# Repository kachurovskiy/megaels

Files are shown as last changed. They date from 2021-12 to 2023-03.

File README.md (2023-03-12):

**This software and instructions are provided as is, without warranty of any kind. This is a hobby project. Using this might damage your equipment, cause injury or death. Use at your own risk. Original author didn't state the lisence for the code so it remains unknown.**

# MegaEls

Metal lathe electronic lead screw project built on top of Russian-speaking [DigitalFeed ELS system by Oleg A. and contributors from ChipMaker.ru](https://www.chipmaker.ru/topic/118083/).

megaels-example

## ⚡ Looking for resellers and manufacturers 💲

If you're willing to manufacture this device and/or sell it as a kit, we'd be happy to link to your page for free - especially if it makes the build cheaper than buying all the components separately.

## Code

Code is provided in the [folder above](https://github.com/kachurovskiy/megaels/tree/main/Digital_Feed_7e2). It requires tuning a few constants at the top of `Digital_Feed_7e2.ino` to fit your lathe and motors.

Verify that hardware parameters are set correctly:

- Use `mm/min` mode and a clock to ensure each axis moves in the right direction and by the expected amount of mm within 60 seconds
- Use "Dividing head" mode (last one) to check that when you turn the spindle by hand in the "forward" direction, angle on screen increments from 0 to 360

Every time hardware parameters change, update `Cone_Info` and `Thread_Info` tables in the middle of that file using calculator in [`tables.html`](https://kachurovskiy.github.io/megaels/Digital_Feed_7e2/tables.html). If you don't recalculate those tables, your threads and cones will come out wrong even when `mm/min` and dividing head tests above pass.

To upload the code to your device, install Arduino IDE, connect your Arduino Mega to the computer via a USB cable, open `Digital_Feed_7e2.ino`, select `Arduino Mega 2560` in `Tools > Board` and click `Sketch > Upload`.

## PCB

megaels_2012-12-05

[Gerber files for production](https://github.com/kachurovskiy/megaels/raw/main/PCB_20211205/Gerber_PCB_MegaEls_20211205.zip)

Some PCB production techniques use lead and other nasty stuff. Order at your own risk and dispose properly.

Ordering it from JLCPCB.com takes just a few clicks - upload the ZIP file, use all default settings, choose shipping and checkout. Costs around 20 euro with delivery for 5 PCBs (minumum order).

## Components

- [Arduino Mega 2560](https://www.aliexpress.com/item/32850843888.html) (micro USB)
- [Connector pins](https://www.aliexpress.com/item/1005002577212594.html) that would get soldered to the board
- [1602 LCD 5V](https://www.aliexpress.com/item/32326489466.html)
- [9 6\*6 push buttons](https://www.aliexpress.com/item/32862548214.html)
- [8-position switches](https://www.aliexpress.com/item/4000700310059.html)
- [Manual pulse generator 5V 4-pin 100 pulses](https://www.aliexpress.com/item/32949618549.html) 60mm
- [4-position joystick with latching and a button](https://www.aliexpress.com/item/4000893010190.html) though this one is a little too big and hard to switch
- [2 RV09 10kOhm potentiometers](https://www.aliexpress.com/item/4000078097697.html)
- [KF2EDG connectors with 3.5mm pitch](https://www.aliexpress.com/item/1005003085954456.html) - 5 with 4 pins, 1 with 6 pins, make sure to order both plug and straight needle
- [4 1kOhm resistor arrays with 8 resistors each](https://www.aliexpress.com/item/32840103807.html)
- 2 1kOhm resistors and 4 680 Ohm resistors
- 5V buzzer
- 2 ceramic capacitors e.g. 10 uF
- 4 LEDs

## Cases

The following cases are designed to be used with [M3 threaded inserts](https://www.aliexpress.com/item/32430148405.html) that would be pushed into the 4 designated holes using your soldering iron tip and receive M3 [nylon screws (for MPG) or 20mm standoffs (for the main case)](https://www.aliexpress.com/item/32617866125.html). 

### Main case

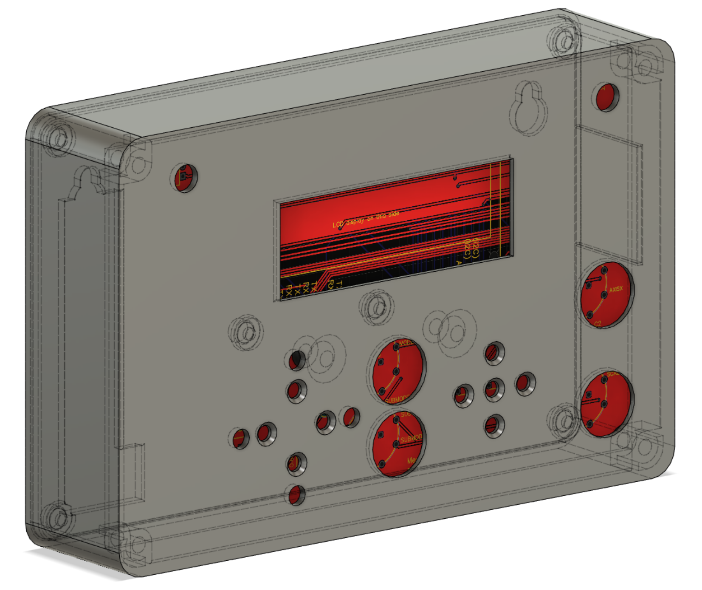
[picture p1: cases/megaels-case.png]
megaels_2012-12-05


Here the lid is connected using nylon screws into 20mm standoffs that work as screws holding the PCB down. It's designed to be mounted using two M5 bolts 135mm apart on centers.

Cut 1 line on the right side of the case and push the small part of the wall to the outside to get access to the mini USB port of the Arduino.

Download: [STL body](https://github.com/kachurovskiy/megaels/raw/main/cases/megaels-case-body.stl) and [STL lid](https://github.com/kachurovskiy/megaels/raw/main/cases/megaels-case-lid.stl) or [f3d](https://github.com/kachurovskiy/megaels/raw/main/cases/MegaElsCase.f3d)

[Printable SVG](https://github.com/kachurovskiy/megaels/raw/main/megaels-face.svg) with labels for the controls.

### MPG case

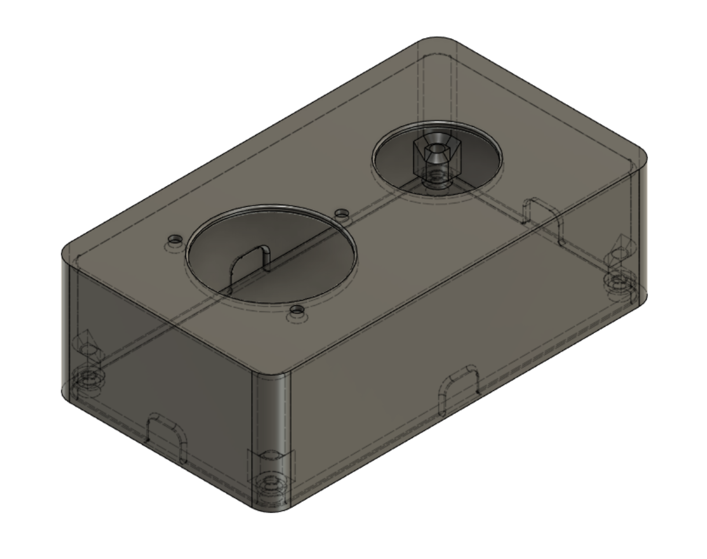
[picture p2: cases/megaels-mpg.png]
megaels_2012-12-05


Download: [STL body](https://github.com/kachurovskiy/megaels/raw/main/cases/megaels-mpg-body.stl) and [STL lid](https://github.com/kachurovskiy/megaels/raw/main/cases/megaels-mpg-lid.stl) or [f3d](https://github.com/kachurovskiy/megaels/raw/main/cases/MegaElsMPG.f3d)

## Schematics

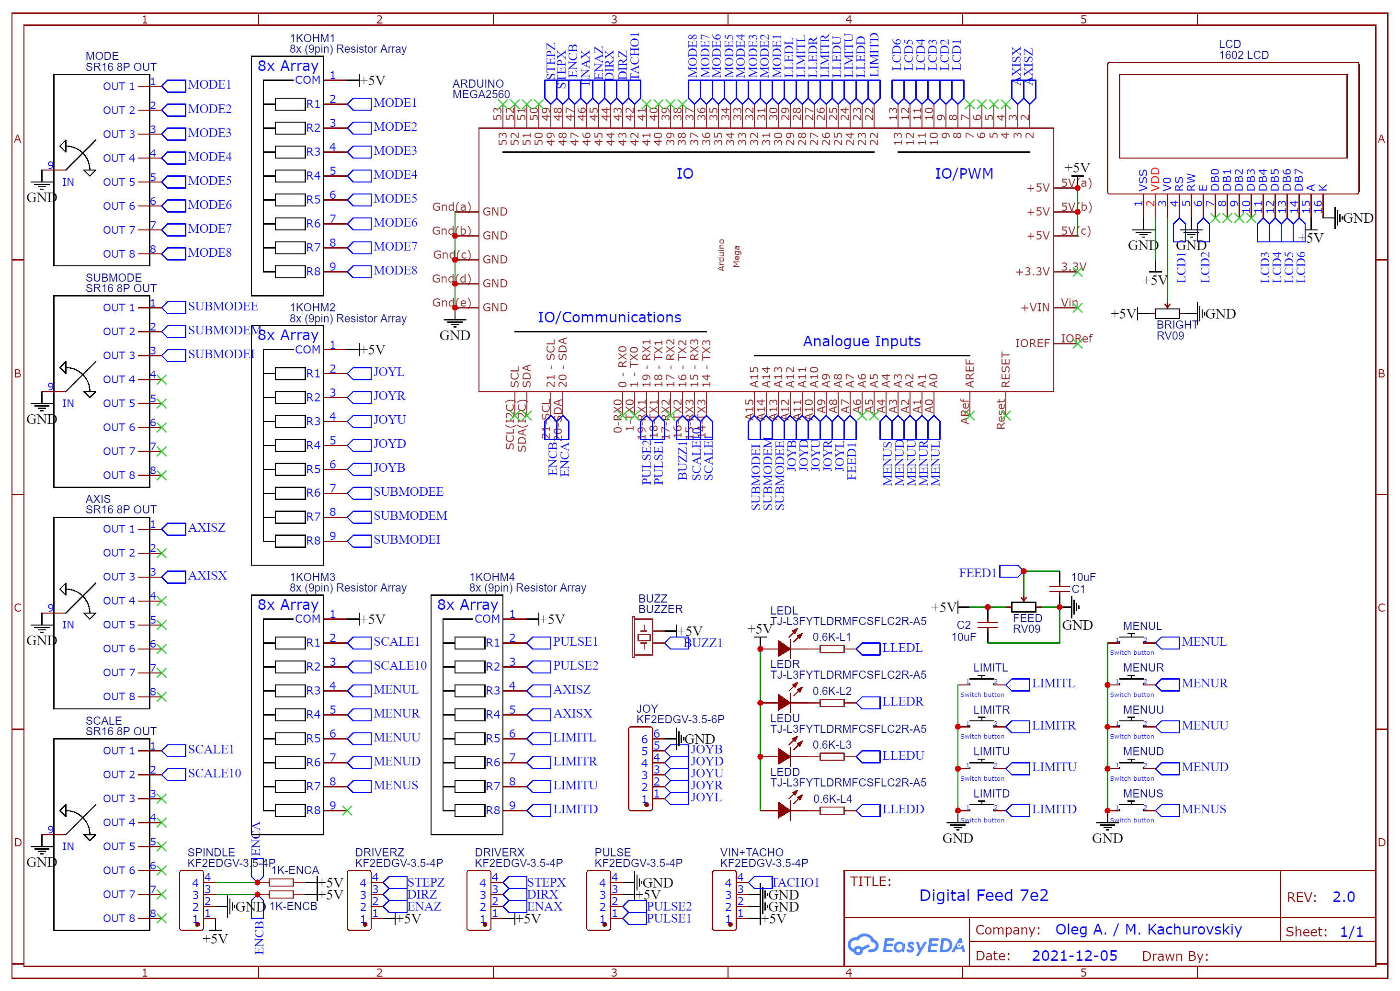
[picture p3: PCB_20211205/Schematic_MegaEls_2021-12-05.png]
MegaEls schematics


## Quick Start

### Moving the tool

- Select `Z` or `X` axis using the corresponding switch
- Select `1x` or `10x` scale using the corresponding switch
- Rotate the handwheel

https://user-images.githubusercontent.com/517919/150657985-6fe1d571-e0b5-475b-9b13-4543c2c39b69.mp4

1 impulse from the handwheel should correspond to 0.01mm movement of the motor in `1x`, 0.1mm in `10x`. If the motor doesn't move, try switching to submode to manual or switching mode to a different value.

### Turning of facing

https://user-images.githubusercontent.com/517919/150658372-34b87c6c-d6d8-46ef-8bb0-31651cf59bb8.mp4

- Set mode to `Feed mm/rev`
- Set submode to manual
- Start the spindle
- Use joystick to start/stop feeding into any of the 4 directions
- Use the top-left potentiometer to change the speed

### Asynchronous feed (grinding)

https://user-images.githubusercontent.com/517919/150658051-4663ad40-8815-415f-8046-cac0e11eda6a.mp4

- Set mode to `Feed mm/min`
- Set submode to manual
- Use joystick to start/stop feeding into any of the 4 directions
- Use the top-left potentiometer to change the speed.

### Threading

Using the right-hand thread cut to the chuck as an example:

https://user-images.githubusercontent.com/517919/150672370-4f7bad88-6a53-406b-a333-fa034ceace00.mp4

- Set mode to `Thrd`
- Set submode to manual
- Use up/down menu buttons to select the pitch. For TPI pitches, scroll up through all the metric pitches.
- Move the tool using the handwheel to the left-most `Z` position
- Set the left limit using the corresponding button
- Move the tool using the handwheel to the right-most `Z` position
- Set the right limit using the corresponding button
- Start the spindle
- Move in the cutter (manually or using the handwheel)
- Set joystick to "left" and wait for the tool to reach the left limit (don't stop the spindle)
- Move the cutter out
- Set joystick to "right" and wait for the tool to reach the right limit (don't stop the spindle), use joystick button for faster movement
- Move in the cutter
- Set joystick to "left" and so on

### Automatic threading

Using the right-hand thread cut to the chuck as an example:

https://user-images.githubusercontent.com/517919/150673123-4970087e-299d-4873-bf87-a3d265480593.mp4

- Set mode to `Thrd`
- Set submode to manual
- Use up/down menu buttons to select the pitch. For TPI pitches, scroll up through all the metric pitches.
- Move the tool using the handwheel to the left-most `Z` position
- Set the left limit using the corresponding button
- Start the spindle
- Move the tool using the handwheel so that the cutter just barely touches the material
- Move the tool using the handwheel to the right-most `Z` position
- Set the right limit using the corresponding button
- Set submode to external
- Set joystick to "left" and wait for the operation to complete

When done, set joystick to neutral and submode to manual to be able to use the handwheel again.

#### Manual follow-up after automatic threading

When automatic threading is finished you can test fit and potentially make a few more passes:

https://user-images.githubusercontent.com/517919/150681412-96608c69-1e91-40f1-9b8f-9cf68e4d7d45.mp4

- Move joystick to neutral
- Set submode to manual
- Set joystick to "right" and press the joystick button to move past the right limit
- Turn on the spindle (no need to reverse it) and wait for the cutter to move out of the way, turn off the spindle
- Test fit the part
- Set joystick to "left"
- Turn on the spindle, move in the cutter, make another pass, it should stop at your existing left stop
- Move out the cutter, no need to stop the spindle
- Set joystick to "right", it should stop at your existing right stop, repeat until the part fits

### Cones

https://user-images.githubusercontent.com/517919/151621173-53c0f2e1-b2ff-46d9-8cfa-94ba974be943.mp4

- Set mode to `>` or `<`
- Set submode to manual
- Pick the cone angle using the menu buttons
- Turn on the spindle
- Use joystick "left" and "right" positions to move the cutter along the cone
- Use joystick "forward" and "back" positions to move the cutter in or out

## Manual

There are [some instructions explaining how to operate the ELS](https://github.com/kachurovskiy/megaels/blob/main/Digital_Feed_7e2/manual.md) that I auto-translated and corrected a bit but expect to invest some time here :)

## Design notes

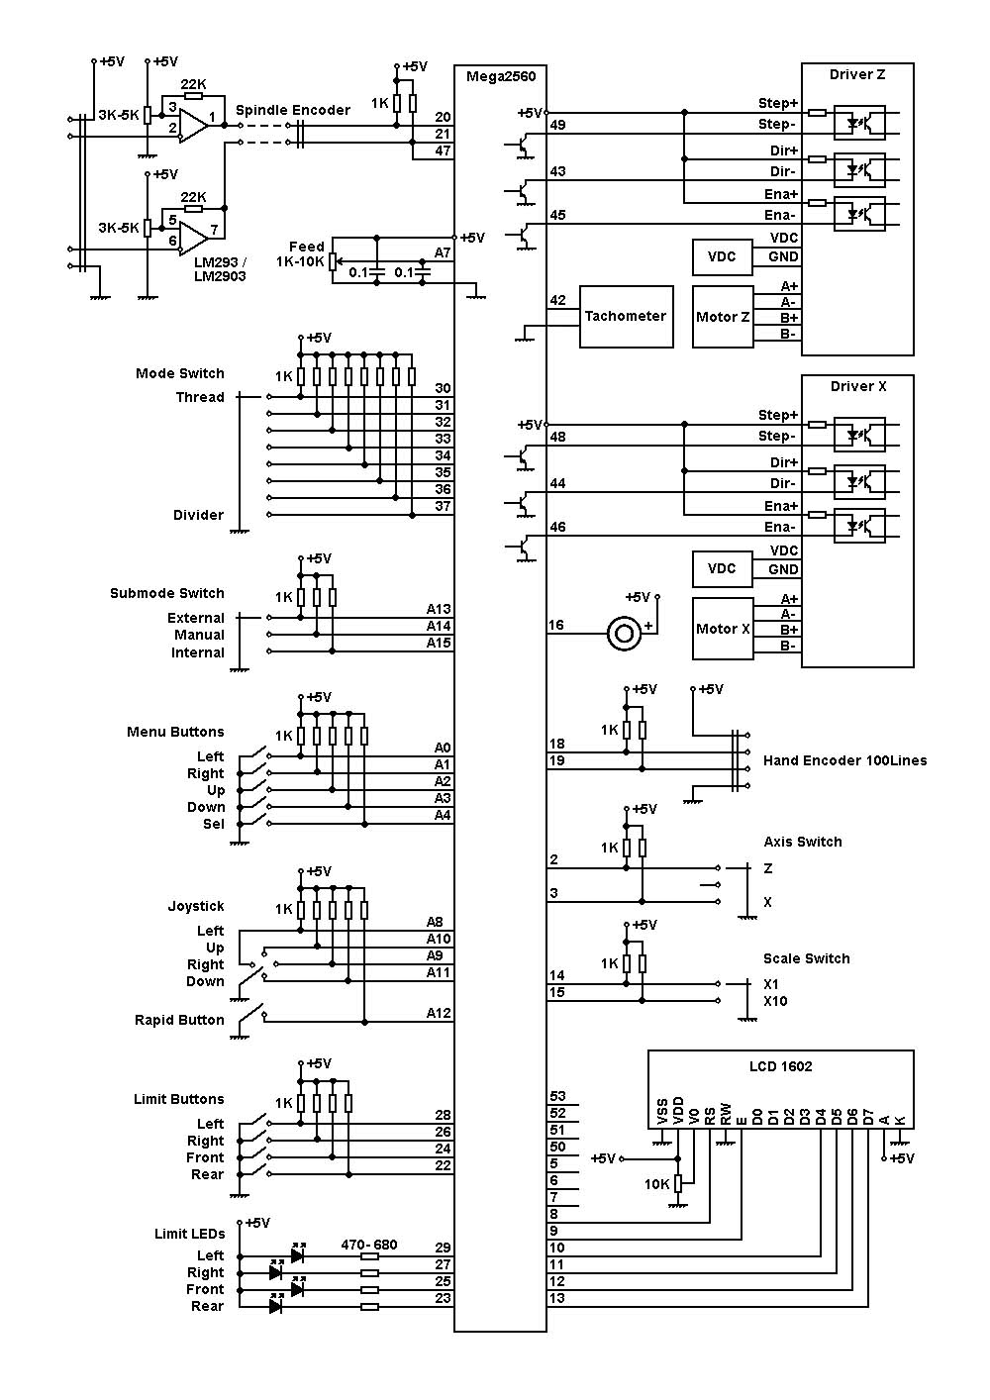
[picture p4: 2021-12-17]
Digital_Feed_7e2/!_ELS_V7.jpg

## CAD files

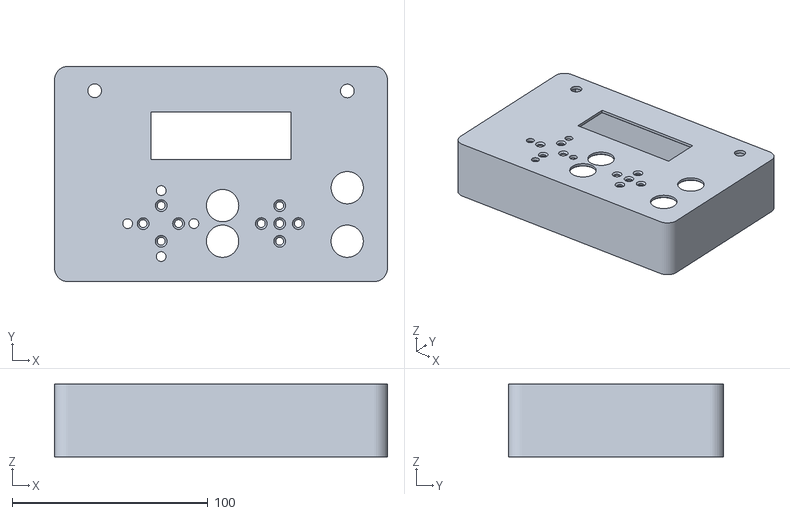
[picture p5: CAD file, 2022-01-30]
cases/megaels-case-body.stl
170.0 x 110.0 x 37.1

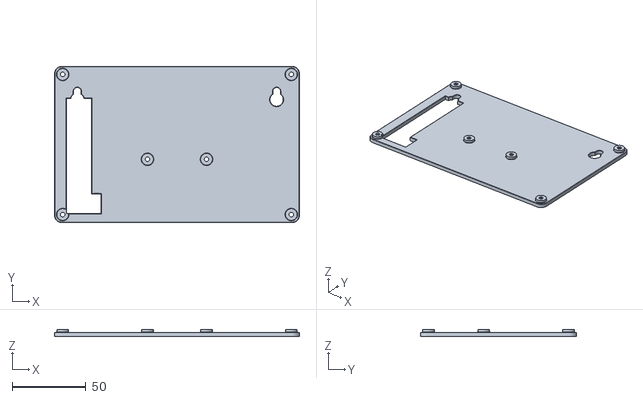
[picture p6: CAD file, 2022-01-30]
cases/megaels-case-lid.stl
166.0 x 106.0 x 5.00

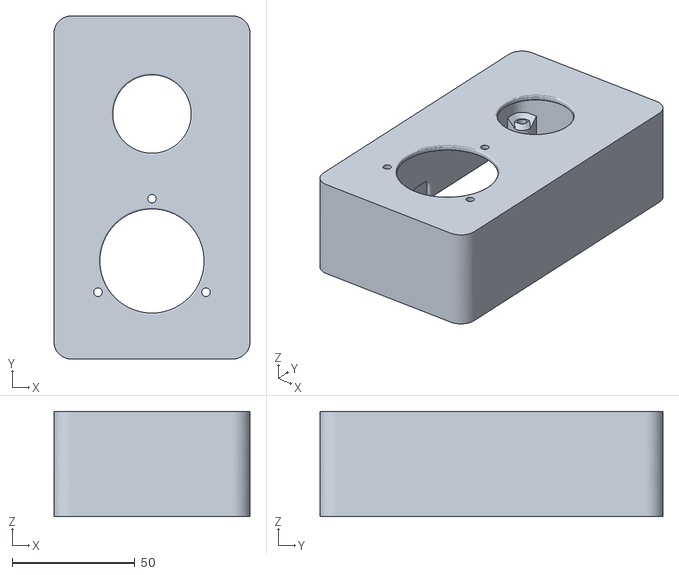
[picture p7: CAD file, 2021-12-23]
cases/megaels-mpg-body.stl
80.0 x 140.0 x 43.0

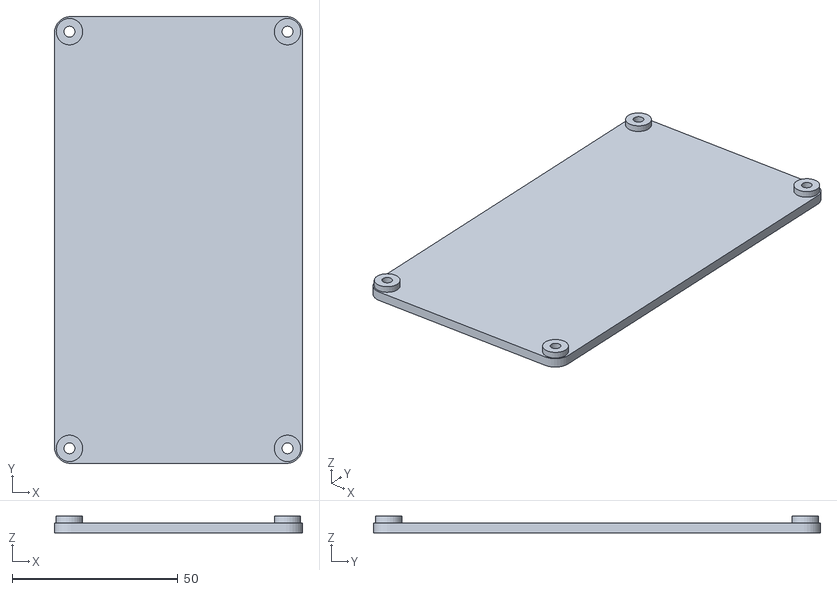
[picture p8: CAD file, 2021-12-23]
cases/megaels-mpg-lid.stl
75.0 x 135.0 x 5.00

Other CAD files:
cases/MegaElsCase.f3d
cases/MegaElsMPG.f3d

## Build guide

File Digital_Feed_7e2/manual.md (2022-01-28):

# Digital Feed Electronic Lead Screw 7e2 Manual

Note: this is a slightly redacted automated translation of a manual written by Oleg A. and contributors from ChipMaker.ru. Use with caution.

## Basic concepts and definitions

**Limits** (electronic stops) are virtual positions on the workpiece that limit the machining area (movement ranges tool) and operate in different modes of operation. There are left, right, front and back limits. 

The positions of the limits are set only with the middle (neutral) position of the joystick and the position of the "Submode" switch "Manual". 

Note: the distance between the limits (processing zones) cannot be less than some values determined by your equipment and firmware parameters (the distance between the limits cannot be less than the "acceleration + deceleration" accelerated).

**Feed** is a value that characterizes the speed of the tool along or across the workpiece. Depending on the mode of operation, synchronous or asynchronous, it is measured in millimeters per revolution or millimeters per minute.

**Rapid feed** is the mode of tool movement with the maximum possible speed along one of the axes. It is activated by pressing a special fast travel button on the joystick. Rapid feed is not activated or the movement does not start at all when the distance from the current position of the tool to the stop on the side of movement is less than the distance required for acceleration and deceleration.

## Controls

### Tuning

Intended for selecting the operating mode and setting the mode parameters:

- 8-position mode switch
- 3-position submode switch
- Buttons - up / down / right / left / select to select and change parameter values

### Operational

Directly for operation:

- 4-position joystick with position fixation and its "rapid feed"
- Button 4 buttons for setting / removing limits (left / right / front / rear)
- Potentiometer, which sets the amount of feed to the manual pulse generator (popularly RGI, Handcoder) - 100 pulses per revolution and its satellite switches:
  - 3-position - axis selection: Z / inactive / X
  - 2-position - selection of the scale of movement: 0.01mm / 0.1mm per one "click" of the RGI.

## Basic operating modes

### Thread

- With spindle reversal without opening the mother nut (no limits)
- Without reversing and without opening the nut, switching the direction of the joystick (limits must be set)
- Without reversing with opening the nut and manual return (synchronization by the threaded indicator)
- Automatically (see below)

When preparing and setting the parameters:

- Use the Up-Down buttons to select the thread pitch, can be changed only when the joystick is in a neutral position
- 4 thread directions along the joystick
- 4 limit buttons, limits are set only when the joystick is in neutral position

When the joystick button is pressed, the right stop is ignored, you can arbitrarily ride after it and try on the counterpart, to restore synchronization, it is enough to enter the zone between the limits and reach the right stop, continue threading as usual.

### Automatic threading

1. Prepare outside/inner diameter to the starting size (e.g. 12mm for M12)
2. Set the right and left stops to the required thread length
3. In the "Thread" mode, use the Up / Down buttons to select the required pitch
4. With the "Submode" switch, select "External" Ext or "Internal" Int
5. On the example of a right-hand thread, direct spindle turns, cut to the chuck:
   1. before starting, touch the workpiece with a threaded cutter in diameter and set the carriage to the right stop (limit),
   2. switch the joystick to the left, the process has started, the cross stops light up alternately , the cross stops are extinguished - the process is complete.
6. When done, tool moves to the starting position

**When cutting 55 degree thread, do not use the automatic threading** - or use the machine 2 times in a row, having previously recalculated the height of 55 degree and 60 degree triangles for the current step, before the second pass of the machine, apply the difference in depth manually.

### Multi-start thread

After cutting the 1st thread:

1. Move the cutter to the starting position (in automatic mode, the cutter will take the starting position itself)
2. Stop the spindle
3. Switch to the "Divider" mode
4. Turn the spindle to set the displayed angle to 180 degrees
5. Reset the angle with the "Sel" button
6. Return to the "Thread" mode
7. Start the spindle
8. The 2nd thread will be cut with an offset of 180 degrees relative to the 1st
9. For a 3-way entry - reset accordingly after 120 degrees, etc.

### Synchronous feed (mm / rev)

- 4 directions of feed on the joystick
- 4 directions of rapid movement on the joystick and the button of the accelerated
- 4 buttons of the limit, the limits are set only with the neutral position of the joystick and manual submode

Use the potentiometer on the top-left to change the amount of feed (even during the operation).

### Automatic multi-pass synchronous feed (mm / rev)

Same as "Synchronous feed" but also:

- Use the Up / Down buttons to set the removal rate `Ap`
- Use the Right / Left buttons to set the number of passes `Pq`

Total amount of material removed is `Pq * Ap * 2`.

#### External groove, direction to the chuck

In the "Manual" mode set the right + left limits, move the instrument to the right limit, the "Submode" switch to the "Ext" position, switch the joystick "Left". 

#### External groove, direction from the chuck

In "Manual" mode, set the right + left limits, move the tool to the left limit, switch "Submode" to the "Ext" position, switch the joystick "Right".

#### Internal boring, direction to the chuck

In "Manual" mode set the right + left limits, move the tool to the right limit, switch "Submode" to "Int", switch the joystick "Left".

#### Internal boring, direction from the chuck

In the "Manual" mode set the right + left limits, move the tool to the left limit, switch the "Submode" switch to the "Int" position, switch the joystick "Right".

#### Facing, direction to the spindle axis

In the "Manual" mode, set the front + back limits, move the tool to the back limit, the "Submode" switch to the "Ext" position, switch the "Forward" joystick.

#### Facing, direction from the spindle axis

In the "Manual" mode, set the front + back limits, move the tool to the front limit, the "Submode" switch to the "Ext" position, switch the "Back" joystick.

### Asynchronous feed (mm / min)

- 4 directions of feed along the joystick
- 4 directions of fast movement along the joystick and the accelerated button
- 4 buttons of the limit, the limits are set only with the neutral position of the joystick and neutral the position of the switch "Submode"

Use the potentiometer on the top-left to change the amount of feed (even during the operation).
 
### Automatic multi-pass asynchronous feed (mm / min)

Experimental.

### Cone left and right (Cone < and Cone >)

- Use the Right-Left buttons (with the joystick neutral position) to select the cone.
- The front-back limits (if they were set earlier) are ignored, but their position in memory is retained.
- Cutting is switched on by Joystick Right / Left.
- The joystick button is used to accelerate movement, the trajectory is the selected cone.
- Joystick forward / reverse switching enables synchronized feed in the corresponding direction.

Sharpen the inner cone from a smaller diameter to a larger one, gradually going deeper into the previously prepared hole. Sharpening from the chuck.

Sharpen the outer cone from a larger diameter to a smaller, larger diameter at the chuck.

The exception is the adapter, in this case, too, from a larger diameter to a smaller one, but the chuck has a smaller diameter and is cut in advance.

In this case, the backlash of the screws is taken out and both screws will always be loaded by the feed.

This principle is used to build an Automaton on cones. 

#### Automatic cone

3 variations are available:

- outer cone (thick at the chuck) cut from left to right
- outer cone (thin at the chuck, you need a technological cut along the left end), cut it from right to left, before the technological groove
- inner cone (thin at the chuck) cut it from left to right

### Reserve

Empty for now.

### Rough sphere (Sphr)

Tool - a cut-off tool with a straight cutting edge.

- Using the Up / Down buttons set the diameter of the ball,
- Use the Right / Left buttons to set the residual diameter of the leg,
- With the "Sel" button pressed, set the width of the cutter
- With the "Sel" button pressed, buttons Right / Left set the width steps (step Z)

Procedure:

1. Cut through the workpiece in diameter future sphere + D which must be greater than X backlash and less than REBOUND_X
2. Use parting tool
3. Cut through the workpiece for the convenience of measurements, but no more than ⅓ of the given diameter is not clear in Z or X (with a cutting tool) with measurements in the required diameter of the future ball
4. Engage the rear support
5. Butt the workpiece (dust the end)
6. Return to the back stop
7. Activate the right stop
8. Switch the joystick to the left
9. Wait end of the process
 
### Division of a circle - divider calculator

The first line of the indicator displays the number of division sectors and the required angle for the current sector (Req). The number of division sectors (maximum 255) is set by the Up-Down buttons.

The second line of the indicator displays the number of the current sector, and the real angle of the spindle. Moving between sectors is carried out with the Right-Left buttons.

All that is required is to turn the spindle to match the readings.

Angle zeroing, if necessary, is performed by the 5th menu button.
 
2 short "beeps" in automatic modes means: "I am working", do not put your hands into the rotating mechanism and wait for the end of the process.

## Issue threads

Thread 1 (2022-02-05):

x cross slide questions

pantonvich, 2022-02-05:
question on tables.html - and in general - on my x axis how do I account for the gear ratio from the x-stepper to cross slide screw pitch.
From your thingverse cross slide - it looks like you have a 3x - 54/18 but I'm not seeing that in the digital_feed_7e2 or tables.html code that you have posted. I have a 1mm cross slide but an odd 77/13. I started my els about a year ago and just started working on it again last month. I found your github in the last two weeks - so thanks for posting what you have. I'm not that good with github - so not sure how to correctly tag this

gerritv, 2022-02-05:
You need to calculate the number of steps to revolve the leadscrew one revolution. The motor is usally 200 steps/rev, add in the 77/13 ratio (5.923) to get 1184.6 steps per rev?

pantonvich, 2022-02-05:
thats what I was thinking so I tried setting MOTOR_X_STEP_PER_REV to 1185. I also tried setting the SCREW_X to 17 with motor 200 - but got an error - see below - looks like if I set the MxStep_X to 1 it's not an issue - so I'll try that.

Digital_Feed_7e2:55: error: static assertion failed: Ð?ÐµÐ²ÐµÑ€Ð½Ð¾ Ð·Ð°Ð´Ð°Ð½Ð¾ Ð·Ð½Ð°Ñ‡ÐµÐ½Ð¸Ðµ MAX_FEED
 static_assert(f > 1, "Ð?ÐµÐ²ÐµÑ€Ð½Ð¾ Ð·Ð°Ð´Ð°Ð½Ð¾ Ð·Ð½Ð°Ñ‡ÐµÐ½Ð¸Ðµ MAX_FEED");

kachurovskiy, 2022-02-05:
I prefer changing the leadscrew pitch - using 1:3 reduction on cross-slide with 1.25mm screw I've entered 42 as SCREW_X. That gives something like 1% of error on cross-slide movements in theory but I'll think of something when it becomes a problem 😄

Getting MAX_FEED error means that system wants you to reduce your MAX_FEED constant value (line 23). I believe validation errors like this ensure that the system has time to issue the stepper pulses in all conditions.

kachurovskiy, 2022-02-05:
Another option to make MAX_FEED validation happy is to reduce micro-stepping e.g. from 800 steps per revolution to 400 - or so I believe.

pantonvich, 2022-02-05:
I set it to 200 i.e 1 and and changed the driver to 200- I'm trying to verify what movement I get with 100 clicks from the handcoder ...

pantonvich, 2022-02-05:
so with
#define MOTOR_X_STEP_PER_REV 1185      // X motor steps (cross-slide) - almost always 200, microsteps configured below
#define SCREW_X              100
#define McSTEP_X             1

I get 1mm on the x axis for 100 clicks of the hand coder - is that what I should expect?

kachurovskiy, 2022-02-05:
> I get 1mm on the x axis for 100 clicks of the hand coder - is that what I should expect?

Yes. Or 10 clicks on 10x resolution.

Closed 2022-02-22.

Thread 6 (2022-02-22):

Réglage des paramètres

Dididu12, 2022-02-22:
I come to you because I want to know the different parameters that must be set in the code and what are the different settings for in the photo below. For example:

SCREW_X (42) ??
MOTOR_X_STEP_PER_REV ??
REBOUND_X ??
REBOUND_Z ??

my turn and the same as kachurovskiy if I do the calculation of the x axis so 54/18= 3. (One complete engine revolution =200) So 3x200=600 MOTOR_X_STEP_PER_REV=600??

As soon as I change its parameters MAX_FEED starts to growl He and yet set to 20

I hope here someone can help me thank you
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

pantonvich, 2022-02-22:
He adjusted screw_x. If you make rev =600 adjust screw_x to pitch of screw likely 1mm so set it to 100. Also you might need to set McSTEP_x to 1 - you will need to set the stepper driver to the same. If code still errors out adj the Max_Feed to a lower number. The point of the check is to not overwhelm the stepper motor with steps it can keep up with.

kachurovskiy, 2022-02-22:
Dilan, what is your main and cross-slide leadscrew pitches? Mine are 2.0mm and 1.25mm. Knowing that and your 3:1 reduction on the cross-slide we should be able to tell you which values to put in the code and on stepper drivers. Thank you.

Dididu12, 2022-02-22:
The main screw and 2mm and 1mm for cross carriage

kachurovskiy, 2022-02-22:
Try the following:

```
#define MOTOR_Z_STEP_PER_REV 200      // Z motor steps (leadscrew) - almost always 200, microsteps configured below
#define SCREW_Z              200      // Z (leadscrew) pitch, in hundreds of a mm
#define McSTEP_Z             4        // Z driver microsteps (400 steps = 2, 800 steps = 4, etc)
#define MOTOR_X_STEP_PER_REV 200      // X motor steps (cross-slide) - almost always 200, microsteps configured below
#define SCREW_X              33       // 1.00mm via 3:1 reduction
#define REBOUND_X            200      // X backlash in microsteps
#define REBOUND_Z            200      // Z backlash in microsteps
#define McSTEP_X             2        // Z driver microsteps (400 steps = 2, 800 steps = 4, etc)
```

You would need to also set the main leadscrew driver to 800 steps and cross-slide driver to 400 steps and update tables via [tables.html](http://kachurovskiy.com/megaels/Digital_Feed_7e2/tables.html).

Dididu12, 2022-02-23:
I'm trying this weekend thank you I'll keep you posted on the progress thank you 🤝👍🏼

Dididu12, 2022-02-26:
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
on the construction diagram I do not quite understand how the card is powered. I guess it's with the green terminals, which I can't translate well, the same for the pulse generator and the joystick, which wire goes where?? thank you very much for your help I soon finished assembling the map print

kachurovskiy, 2022-02-27:
> MY QUESTION: CAN I LEAVE IT AS IS?? ITS INFLUENCE ON WHICH SETTING THANK YOU

I think yes for now.

> which wire goes where?

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

> pulse generator

Your pulse generator should have 4 terminals - 5V, ground, and 2 signal lines. Connect them correspondingly to 5V, ground and 2 remaining pins in the 5th terminal block (counting from the top).

> joystick

For the joystick that is recommended for the build, you need to connect together the wires so that clicking the joystick button or switching it in a given direction connects the corresponding pin on the 6th terminal block to the GND.

E.g. leaning joystick to the left should result in the following 2 pins getting connected:

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

Dididu12, 2022-02-27:
Thank you for your help I think I have understood everything now it's a great job again thank you

Dididu12, 2022-03-01:
Hello everyone before assembling my print card I wanted to test the stop LEDs it turns out that there is one that does not light up the bottom one how to test it in operation with the m card

Dididu12, 2022-03-19:
hello I have just tested the operation of the card it turns out that it does not work as expected I do not know why I have respected the connections well I hope to find a solution

Dididu12, 2022-03-19:
https://user-images.githubusercontent.com/97460665/159134854-392a5770-ab21-449f-872d-c335e52fd27b.mp4

Dididu12, 2022-03-19:
is there a way to weld the yellow resistors and the long black ones thank you

kachurovskiy, 2022-03-19:
Dilan, can you please post the photos of your soldered PCB top and bottom sides? Some easy pitfalls:

- Soldering 10-leg resistors array wrong way
- Soldering LEDs wrong way

What about 8-position switches - do they work as intended? Also, brightness and feed potentiometers?

Dididu12, 2022-03-19:
Je vous envoie la photo demain merci pour la réponse 👍🏼

Dididu12, 2022-03-19:
There is not much that works the stops do not work the 8 position works when they want and the division mode is missing too

Dididu12, 2022-03-19:
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

Dididu12, 2022-03-20:
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

the joystick button doesn't work

kachurovskiy, 2022-03-20:
Dilan, looks like you've soldered the 9x resistor arrays the wrong way? IIRC the dot on the array should be over the square hole on the PCB. In other words, resistance between square hole and all other holes should be 1kOhm.

Dididu12, 2022-03-20:
yes the problem was there but on the other hand the leds do not light up when you press the button any idea??

kachurovskiy, 2022-03-20:
That is expected when the resistor array is connected incorrectly.

Dididu12, 2022-03-20:
this also happens with array resistors in the right direction so it doesn't work yet??

kachurovskiy, 2022-03-20:
Dilan, were you able to de-solder all 40 pins and swap the resistor arrays around? Can you post a photo of how it looks now? Many thanks.

Dididu12, 2022-03-20:
ok I'm not at home my evenings I send you his thank you and yes I unsoldered and exchanged the black resistors

Dididu12, 2022-03-20:
Everything seems to be back to normal, however the sphere mode does not work, that's normal

Dididu12, 2022-03-21:
Hello I have just noticed that the stops are reversed especially the axes how to fix this thank you

kachurovskiy, 2022-03-21:
Dilan, it sounds like you need to check the settings:

1. Go into the last mode (where the spindle angle is shown on screen) and rotate the spindle normally. Angle on screen should increment from 0 to 360 when you make a full turn of the spindle by hand.
2. Go into `Feed mm/min` mode, ensure both axes more in the correct direction. E.g. joystick right results in Z moving right. If not, adjust `Z_INVERT`.
3. Go into `Feed mm/min` mode, use the top-left knob set the speed to e.g. `50`, set joystick to right, use a ruler to ensure the carriage moves 50mm within 60 seconds. Same for X axis. If not, adjust parameters at the top of `Digital_Feed_7e2.ino` until it works.
4. Finally, re-calculate the tables using `tables.html`

Dididu12, 2022-03-22:
ok I'll do it in the weekend I'll let you know

Dididu12, 2022-03-25:
hello my problem and the following the x axis and reverse how to make it rotate in the right direction thank you

Dididu12, 2022-03-25:
![Uploading 16482323569722772504916710016242.jpg…]()

Dididu12, 2022-03-25:
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

Dididu12, 2022-03-25:
I just understood something I realize that as the x axis is inverted this is the problem that's why it doesn't take material it comes back much further each time

kachurovskiy, 2022-03-26:
Dilan, I don't think there's a way to invert X at the moment in the code. Looks like so far no one needed that. Wonder if you happen to have a "reverse" switch on your stepper driver?

Dididu12, 2022-03-26:
I just have the x axis which is reversed I don't know why the connections are well done what to do thank you

gerritv, 2022-03-26:
you can reverse the direction of the motor by exchanging 2 wires, e.g. wires 1 and 2 coming out of the motor.

Dididu12, 2022-03-26:
I tried reversing the wires, it didn't change anything.

gerritv, 2022-03-26:
that is not possible. There are 2 coils in the motor, swapping the two wires for one coil reverses its direction.

Dididu12, 2022-03-26:
ok but which one to exchange do you have a photo thank you

gerritv, 2022-03-27:
This sketch shows wiring in the motor. You need a meter to determine the pairs. (don't worry about which is A or B.) Connect the pairs to controller. To reverse the motor
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
 direction, swap A and A- wires, or B and B- wires.
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

Dididu12, 2022-03-27:
I changed the wiring and it still turns in the same direction, I find it weird?

gerritv, 2022-03-27:
Can you post photo of your X motor and of the stepper driver? And mark what wires you changed?

gerritv, 2022-03-27:
Lets verify the basics on your machine:
1. If you turn handwheel clockwise, the carriage should move toward spindle, Z axis. The cross slide should move toward back of lathe.
2. If you set LH limit, then move carriage to right and set RH limit, moving joy stick to left should move carriage toward spindle. (in Feed asynchronous mode, no need to have spindle turning)
3. In dividing mode, turn top of spinlde toward you, numbers should increase.

Dididu12, 2022-03-27:
it is not possible to reverse the direction of rotation of the x axis with the Arduino code??

Otherwise yes you turn in the right direction with the joystick and the wheel

gerritv, 2022-03-27:
When you cut threads, does the display say Ext or Int?

Dididu12, 2022-03-27:
I'm waiting for the video to be put on youtube and I'll send you the link

The stopper of the x axis and in the wrong place let's admit when I want to put a stopper it is reversed only on the x axis

gerritv, 2022-03-27:
for threading you don't set X limits, only Z

Dididu12, 2022-03-27:
https://youtu.be/b2t2DgLo_qM

Dididu12, 2022-03-27:
when I put the internal thread to make an external surface it works flawlessly, however when I put the button on external it gives me an internal thread so the tool moves away each time

gerritv, 2022-03-27:
Well then that is your answer, the switch is wired backwards :-)

Dididu12, 2022-03-27:
yes but when I wire the stopper in the right place and always in the wrong place

gerritv, 2022-03-27:
Why change the code when the problem is elsewhere? The code works for the author and you are using his board.
If you wire the Ext/Int switch correctly, and the end stops are reversed, then are you certain the left/right limit switches are correct?
Do you have a voltmeter to test with?

Dididu12, 2022-03-28:
yes I have voltmeter to test but I test or thank you very much

Dididu12, 2022-03-28:
if I managed to change the direction of the motor, it would have solved the problem for a while Whatever I do, nothing changes by reversing the wires, I also find it weird

Dididu12, 2022-03-28:
sayer I succeeded everything is working properly I am happy thank you to all those who help me for their trust 🥰😉

Just a quick question and is it possible to make a quarter round at the end of the room with the sphere function??

Closed 2022-03-29.

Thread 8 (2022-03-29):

Table HTML

Dididu12, 2022-03-29:
hello to all I have a small problem with the cone option for example when I want to make a 45 degree cone it is not 45 degrees however the cross carriage moves well 50 m minutes as well as the z axis everything is well entered in the code as it should be my screw of the crossed axis is 1 mm the screw of the z axis is 2 mm the cross axis driver is set to 400 the z axis driver is set to 800 I have a gear ratio on the cross axis of 3:1. I find that on the automatic threading mode it takes form big passes

Again sorry for the translation if it is not good I do with Google 😉 thank you

kachurovskiy, 2022-03-30:
Dilan, if it's not 45 degrees - what is the resulting cone angle exactly? What is the deviation for other cone angles e.g. for 30 degrees?

Also, please post your `Digital_Feed_7e2.ino` as a gist so that we could take a look at the code - https://gist.github.com/

Thank you.

Dididu12, 2022-04-02:
hello Maxime I checked the angle it is 20 degrees instead of 45 degrees so indeed it is not good

https://gist.github.com/Dididu12/6d27bc34b5af3b8faead01b2d5c6ad23

kachurovskiy, 2022-04-02:
Dilan, looks like you need to update the tables in your code as per [tables.html](http://kachurovskiy.com/megaels/Digital_Feed_7e2/tables.html)

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

Here are the table values I got generated for your parameters:

```
const cone_info_type Cone_Info[] = {
  {  0, 6600, "45dg"},
  { 25, 3598, " KM0"}, // 1:19.212
  { 26, 4620, " KM1"}, // 1:20.047
  { 26, 4264, " KM2"}, // 1:20.02
  { 26, 2970, " KM3"}, // 1:19.922
  { 25, 4153, " KM4"}, // 1:19.254
  { 25,  826, " KM5"}, // 1:19.002
  { 25, 3176, " KM6"}, // 1:19.18
  {  5, 2800, " 1:4"}, // 1:4
  {  6, 6000, " 1:5"}, // 1:5
  {  9, 2400, " 1:7"}, // 1:7
  { 13, 2000, "1:10"}, // 1:10
  { 21, 1200, "1:16"}, // 1:16
  { 26, 4000, "1:20"}, // 1:20
  { 31, 6800, "1:24"}, // 1:24
  { 39, 6000, "1:30"}, // 1:30
  { 66,    0, "1:50"}, // 1:50
  { 12,  686, "7:64"}, // 7:64
  {  4, 6961, " 8dg"},
  {  3, 7430, "10dg"},
  {  2, 4632, "15dg"},
  {  1, 1432, "30dg"},
};
```

and

```
const thread_info_type Thread_Info[] = {
  { 12,    0,   3, 9600, "0.25mm", 0.250, 4, " 750rpm"},
  { 10,    0,   3, 3000, "0.30mm", 0.300, 4, " 750rpm"},
  {  8, 5714,   2, 8286, "0.35mm", 0.350, 4, " 750rpm"},
  {  7, 5000,   2, 4750, "0.40mm", 0.400, 4, " 750rpm"},
  {  6,    0,   1, 9800, "0.50mm", 0.500, 4, " 750rpm"},
  {  5,    0,   1, 6500, "0.60mm", 0.600, 4, " 750rpm"},
  {  4, 2857,   1, 4143, "0.70mm", 0.700, 4, " 750rpm"},
  {  4,    0,   1, 3200, "0.75mm", 0.750, 5, " 750rpm"},
  {  3, 7500,   1, 2375, "0.80mm", 0.800, 5, " 700rpm"},
  {  3,    0,   0, 9900, "1.00mm", 1.000, 6, " 560rpm"},
  {  2, 4000,   0, 7920, "1.25mm", 1.250, 7, " 460rpm"},
  {  2,    0,   0, 6600, "1.50mm", 1.500, 7, " 380rpm"},
  {  1, 7143,   0, 5657, "1.75mm", 1.750, 8, " 320rpm"},
  {  1, 5000,   0, 4950, "2.00mm", 2.000, 9, " 280rpm"},
  {  1, 2000,   0, 3960, "2.50mm", 2.500, 11, " 220rpm"},
  {  1,    0,   0, 3300, "3.00mm", 3.000, 15, " 190rpm"},
  {  0, 7500,   0, 2475, "4.00mm", 4.000, 22, " 140rpm"},

  {  9, 4488,   3, 1181, "80tpi ", 0.318, 4, " 750rpm"},
  {  8, 5039,   2, 8063, "72tpi ", 0.353, 4, " 750rpm"},
  {  7, 5591,   2, 4945, "64tpi ", 0.397, 4, " 750rpm"},
  {  7,  866,   2, 3386, "60tpi ", 0.423, 4, " 750rpm"},
  {  6, 6142,   2, 1827, "56tpi ", 0.454, 4, " 750rpm"},
  {  5, 6693,   1, 8709, "48tpi ", 0.529, 4, " 750rpm"},
  {  5, 1969,   1, 7150, "44tpi ", 0.577, 4, " 750rpm"},
  {  4, 7244,   1, 5591, "40tpi ", 0.635, 4, " 750rpm"},
  {  4, 2520,   1, 4031, "36tpi ", 0.706, 5, " 750rpm"},
  {  3, 7795,   1, 2472, "32tpi ", 0.794, 5, " 710rpm"},
  {  3, 3071,   1,  913, "28tpi ", 0.907, 5, " 650rpm"},
  {  3, 1890,   1,  524, "27tpi ", 0.941, 5, " 600rpm"},
  {  3,  709,   1,  134, "26tpi ", 0.977, 6, " 570rpm"},
  {  2, 8346,   0, 9354, "24tpi ", 1.058, 6, " 500rpm"},
  {  2, 5984,   0, 8575, "22tpi ", 1.155, 6, " 450rpm"},
  {  2, 3622,   0, 7795, "20tpi ", 1.270, 7, " 440rpm"},
  {  2, 2441,   0, 7406, "19tpi ", 1.337, 7, " 420rpm"},
  {  2, 1260,   0, 7016, "18tpi ", 1.411, 7, " 380rpm"},
  {  1, 8898,   0, 6236, "16tpi ", 1.587, 8, " 350rpm"},
  {  1, 6535,   0, 5457, "14tpi ", 1.814, 9, " 320rpm"},
  {  1, 4173,   0, 4677, "12tpi ", 2.117, 10, " 270rpm"},
  {  1, 1811,   0, 3898, "10tpi ", 2.540, 11, " 220rpm"},
  {  1,  630,   0, 3508, " 9tpi ", 2.822, 14, " 190rpm"},
  {  0, 9449,   0, 3118, " 8tpi ", 3.175, 16, " 170rpm"},
  {  0, 8268,   0, 2728, " 7tpi ", 3.629, 19, " 150rpm"},
  {  0, 7087,   0, 2339, " 6tpi ", 4.233, 24, " 140rpm"},
};
```

Dididu12, 2022-04-02:
THANK YOU VERY MUCH I ENTER THE PARAMETERS AND I TELL YOU IF IT CORRESPOND!!!

Dididu12, 2022-04-02:
well I have just done the test I am at 35° for 45° on the arduino there is 10° difference I do not know why

kachurovskiy, 2022-04-02:
Dilan, can you please post another gist with your current `Digital_Feed_7e2.ino`? https://gist.github.com/ - thank you.

Dididu12, 2022-04-03:
https://gist.github.com/Dididu12/c48915304ff0e5e1392b54baaea7925d

kachurovskiy, 2022-04-03:
Dilan, most likely there's a problem with cross-slide lead screw settings. Try using `Feed mm/min` at `50` and see if your cross-slide actually moves 50 mm within 60 seconds?

Dididu12, 2022-04-03:
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

Dididu12, 2022-04-03:
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

Dididu12, 2022-04-03:
I just did the 50mm/minute test on the stopwatch set to 1min so it's 57 seconds for 50mm/min

kachurovskiy, 2022-04-03:
Here are the values I'm setting in tables.html based on your hardware parameters:

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

I'm looking at the tables you posted in https://gist.github.com/Dididu12/c48915304ff0e5e1392b54baaea7925d and they don't match what I see in http://kachurovskiy.com/megaels/Digital_Feed_7e2/tables.html

You need to paste `const cone_info_type Cone_Info[] = ...` and `const thread_info_type Thread_Info[] = ...` code blobs from `tables.html` into your code. Did you do that? Thank you.

Dididu12, 2022-04-03:
yes i did as you said thank you

Dididu12, 2022-04-09:
HELLO MAXIME WHAT I NEED TO DO TO RECOVER THE 3 SECONDS OF THE X AXIS. IT IS GOING FASTER THAN IT SHOULD THANK YOU

kachurovskiy, 2022-04-10:
Dilan, I've realized my mistake, you've correctly used 0.33 as your X axis pitch in tables.html calculation and the code you shared in https://gist.github.com/Dididu12/c48915304ff0e5e1392b54baaea7925d looks good.

With regards to the 3 seconds problem during the `Feed mm/min` mode, I think it's not precise enough for us to draw conclusions. Let's try something else: use the MPG wheel to move the X or Z axis a set distance.

- Select 1x switch
- Select Z or X axis switch
- Rotate the encoder wheel some amount until the backlash is taken out
- Zero the micrometer, make sure it's parallel to the axis
- Rotate the encoder wheel 100 clicks

Respective axis should move by 1mm. Try doing this several times for each axis and see if there's a consistent problem for Z or X.

https://user-images.githubusercontent.com/517919/162625971-53bce4ae-0b3b-404e-a04d-fef5175db8a8.mp4

If the problem is there (axis moves too little or too much), try adjusting the respective pitch (200 or 33) up or down until it's fixed?
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
kachurovskiy, 2022-06-16:
Also, very important, don't forget to actually change the steps on the driver to 1600 :) Fixed the problem for me:

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

Dididu12, 2022-06-16:
1-  @kachurovskiy hi why did i set x driver to 1200 should i do the same??otherwise great to have managed to find the problem

2-  I want to share with you the code that contains the update that I translated into French how do you share it thank you?

kachurovskiy, 2022-06-16:
I have 400 steps on x driver and 3x reduction with 1.25 lead screw, so instead of dividing 1.25 by 3 I decided to multiply 400 by 3 - hence 1200 steps :)

kachurovskiy, 2022-06-17:
Dilan, you'd want to set "X driver steps" = 1200 and "X axis pitch" = 1

Dididu12, 2022-06-18:
@kachurovskiy actuellement on avait mis dans table HTML 0.33 pour la réduction de l'axe x et non 1mm ??

kachurovskiy, 2022-06-18:
Since you have 3x reduction, we have 2 options - divide pitch by 3 or multiply X steps by 3.

Dividing pitch introduces 1% error since 0.33*3 = 0.99 and not 1.00.

So, using 1200 steps and 1mm pitch is suggested :)

Dididu12, 2022-06-18:
Ok merci beaucoup j'essaie sa !👍🏼

Dididu12, 2022-06-25:
@kachurovskiy Salut donc je met comme sur la photo ??
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

Dididu12, 2022-06-25:
@kachurovskiy avez vous une photo de réglage de vos driver et un photo de votre réglage sur Arduino merci

Dididu12, 2022-06-27:
@kachurovskiy cela ne fonctionne pas pour moi ou alors j'ai fait une fausse manip

kachurovskiy, 2022-06-27:
Dilan, here are my Arduino settings:

```
#define ENC_LINE_PER_REV     600      // Encoder lines per 1 spindle turn
#define MOTOR_Z_STEP_PER_REV 200      // Z motor steps (leadscrew) - almost always 200, microsteps configured below
#define SCREW_Z              200      // Z (leadscrew) pitch, in hundreds of a mm
#define McSTEP_Z             8        // Z driver microsteps (400 steps = 2, 800 steps = 4, etc)
#define Z_INVERT                      // Comment this line if Z motor is connected directly to the lead screw, uncomment if via belt
// #define Z_ENA_INVERT                  // Comment/uncomment this line if Z motor is getting disabled when it should be enabled
#define MOTOR_X_STEP_PER_REV 200      // X motor steps (cross-slide) - almost always 200, microsteps configured below
#define SCREW_X              125       // X (cross-slide) pitch, in hundreds of a mm
#define REBOUND_X            200      // X backlash in microsteps
#define REBOUND_Z            200      // Z backlash in microsteps
#define McSTEP_X             6        // Z driver microsteps (400 steps = 2, 800 steps = 4, etc)
//
#define THRD_ACCEL           25       // К.деления с которого будем ускоряться на Резьбах, Accel+Ks должен быть < 255
#define FEED_ACCEL           3        // Жесткость разгона на подачах, бОльше значение - короче разгон.
//
#define MIN_FEED             2        // Min feed in 0.01mm. 2 = 0.02mm
#define MAX_FEED             20       // Max feed in 0.01mm. 20 = 0.20mm
#define MIN_aFEED            20       // Min feed in mm/min. 20 = 20mm/min
#define MAX_aFEED            400      // Max feed in mm/min. 400 = 400mm/min

// Rapid feed   
#define MAX_RAPID_MOTION     25                       // Smaller - faster           //16000000/32/((25+1)*2)/800*60=721rpm
#define MIN_RAPID_MOTION    (MAX_RAPID_MOTION + 150)  // Bigger - slower, max 255 //16000000/32/((150+25+1)*2)/800*60=107rpm
#define REPEAt              (McSTEP_Z * 1)            // Repeats for full speed within one step
                                                      // Acceleration duration = 150/2*REPEAT(4)/Microstep(4) = 75 full steps for acceleration
// Manual pulse generator (100 lines)
#define HC_SCALE_1           1        // 1-e положение, масштаб = 1сотка/тик = 1мм/оборот
#define HC_SCALE_10          10       // 2-e положение, масштаб = 10соток/тик = 10мм/оборот
#define HC_START_SPEED_1     250      // старт РГИ, 250000/(250+1)/800*60/2 = 37rpm
#define HC_MAX_SPEED_1       150      // максимум скорости РГИ, 250000/(150+1)/800*60/2 = 62rpm
#define HC_START_SPEED_10    150      // старт РГИ, 250000/(150+1)/800*60/2 = 62rpm
#define HC_MAX_SPEED_10      23       // максимум скорости РГИ, 250000/(23+1)/800*60/2 = 391rpm
#define HC_X_DIR             0        // 1-CW, 0-CCW
```

Drivers - top one is cross-slide, bottom one is leadscrew.

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

What exactly doesn't work?

Dididu12, 2022-06-28:
J'essaie les même réglage et je te dit si sa marche j'espère qu'on i arriveras un jour on est pas très loin du but 😅

Dididu12, 2022-07-03:
Bon sayer j'ai réussi enfin pars contre le moteur de l'axe croisé x vibre énormément

kachurovskiy, 2023-03-12:
Dilan, sorry, don't remember how we resolved this topic but I think your project is successfully completed by now :) Let us know if you have any tips and tricks to share. Thanks!

Closed 2023-03-12.

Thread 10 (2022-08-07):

Tachometer incorrect values

Shiftuia, 2022-08-07:
If switch from tachometer to another mode and then switch mode back - values become incorrect.
Also it will be good to decrease refresh rate of tachometer values

https://user-images.githubusercontent.com/34735272/183307653-02c002ba-15f7-45f7-8428-4eee8d7d1a81.mov

.

kachurovskiy, 2022-08-07:
@Shiftuia I believe that Alex in the video is using a different source code (zzzzzzz8989 as per https://youtu.be/AwgltElphHg?t=449), MegaEls doesn't even have an on-screen tachometer display AFAIK.

Shiftuia, 2022-08-08:
It was first github repo on first of 3 google pages by request "Digital Feed 7e2". I thought, that maybe this repo is 'parent' of other versions. Someone from other versions developers could look here sometimes and see this issue. But I think, that unfortunately other versions are distributed on arduino forums or telegram channels.
You can close that issue if you think that it's non relevant

 Firmware name from video
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

gerritv, 2022-08-08:
This version/variant says it has some tacho support: https://www.chipmaker.ru/files/file/17383/

AFAIK the only development is done via the chipmaker.ru site. Oleg A. is working on a new version but nothing beta released so far.

Shiftuia, 2022-08-09:
Thank! I think it's better to close this issue. It may confuse some other developers.

P.S. still don't understand, why developer from chipmarket doesn't spare his files on any public git hosting...

Closed 2022-08-09.

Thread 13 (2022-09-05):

Resistor arrays

tonywright, 2022-09-05:
In the BOM you have "4 1kOhm resistor arrays with 9 resistors each" but the part that is linked: (https://www.aliexpress.com/item/32840103807.html) has 9 _PIN_ which is 8 resistors and a common isn't it? I hope the link is the correct one as this is what I have ordered :) Just checked and the circuit diagram has the 8 resistors and a common pin.

Tony

kachurovskiy, 2022-09-06:
Good catch, fixed :)

Closed 2022-09-06.

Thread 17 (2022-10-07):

Beeper

tonywright, 2022-10-07:
I'm not getting any Beeps from the Megaels, I assumed that the beeper type is the sort that gives a constant beep sound while power is applied, not the sort that you need to modulate the power to get a frequency? It is polarised which I am sure I got the correct way round. Is there anything else I am missing? Did I assume wrong about the type of Beeper?

kachurovskiy, 2022-10-07:
Tony, please post the picture of your beeper mounted on the PCB and link to the shop where you bought it. Thank you!

tonywright, 2022-10-07:
Here is a pic and yes it is the wrong way round :)
All working now after I have swapped it round.
It was one of the buzzers supplied in one of the Arduino experiment packs of assorted devices.
I hope it is reassuring to anyone else making one of these that all the problems I had (Not many really) were of my own making

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

kachurovskiy, 2022-10-07:
Happy to hear it's resolved, thank you!

Closed 2023-03-12.

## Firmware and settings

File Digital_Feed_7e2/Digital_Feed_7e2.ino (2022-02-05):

#include <avr/pgmspace.h>
#include <util/delay.h>

// Hardware params
// Each time you change these, Cone_Info and Thread_Info tables below must be re-calculated

#define ENC_LINE_PER_REV     600      // Encoder lines per 1 spindle turn
#define MOTOR_Z_STEP_PER_REV 200      // Z motor steps (leadscrew) - almost always 200, microsteps configured below
#define SCREW_Z              200      // Z (leadscrew) pitch, in hundreds of a mm
#define McSTEP_Z             4        // Z driver microsteps (400 steps = 2, 800 steps = 4, etc)
#define Z_INVERT                      // Comment this line if Z motor is connected directly to the lead screw, uncomment if via belt
// #define Z_ENA_INVERT                  // Comment/uncomment this line if Z motor is getting disabled when it should be enabled
#define MOTOR_X_STEP_PER_REV 200      // X motor steps (cross-slide) - almost always 200, microsteps configured below
#define SCREW_X              42       // X (cross-slide) pitch, in hundreds of a mm
#define REBOUND_X            200      // X backlash in microsteps
#define REBOUND_Z            200      // Z backlash in microsteps
#define McSTEP_X             2        // Z driver microsteps (400 steps = 2, 800 steps = 4, etc)
//
#define THRD_ACCEL           25       // К.деления с которого будем ускоряться на Резьбах, Accel+Ks должен быть < 255
#define FEED_ACCEL           3        // Жесткость разгона на подачах, бОльше значение - короче разгон.
//
#define MIN_FEED             2        // Min feed in 0.01mm. 2 = 0.02mm
#define MAX_FEED             20       // Max feed in 0.01mm. 20 = 0.20mm
#define MIN_aFEED            20       // Min feed in mm/min. 20 = 20mm/min
#define MAX_aFEED            400      // Max feed in mm/min. 400 = 400mm/min

// Rapid feed           
#define MAX_RAPID_MOTION     25                       // Smaller - faster           //16000000/32/((25+1)*2)/800*60=721rpm
#define MIN_RAPID_MOTION    (MAX_RAPID_MOTION + 150)  // Bigger - slower, max 255 //16000000/32/((150+25+1)*2)/800*60=107rpm
#define REPEAt              (McSTEP_Z * 1)            // Repeats for full speed within one step
                                                      // Acceleration duration = 150/2*REPEAT(4)/Microstep(4) = 75 full steps for acceleration
// Manual pulse generator (100 lines)
#define HC_SCALE_1           1        // 1-e положение, масштаб = 1сотка/тик = 1мм/оборот
#define HC_SCALE_10          10       // 2-e положение, масштаб = 10соток/тик = 10мм/оборот
#define HC_START_SPEED_1     250      // старт РГИ, 250000/(250+1)/800*60/2 = 37rpm
#define HC_MAX_SPEED_1       150      // максимум скорости РГИ, 250000/(150+1)/800*60/2 = 62rpm
#define HC_START_SPEED_10    150      // старт РГИ, 250000/(150+1)/800*60/2 = 62rpm
#define HC_MAX_SPEED_10      23       // максимум скорости РГИ, 250000/(23+1)/800*60/2 = 391rpm
#define HC_X_DIR             0        // 1-CW, 0-CCW
#define HC_Z_DIR             0        // 1-CW, 0-CCW


//////////////////////////////////////////////////////////////////////////////////////////////////
#define a  (uint32_t)(ENC_LINE_PER_REV / ((float)MOTOR_Z_STEP_PER_REV * McSTEP_Z * MIN_FEED / SCREW_Z) /2 +0.5)
static_assert(a <= 255, "Неверно задано значение MIN_FEED");
#define b  (uint32_t)(ENC_LINE_PER_REV / ((float)MOTOR_Z_STEP_PER_REV * McSTEP_Z * MAX_FEED / SCREW_Z) /2 +0.5)
static_assert(b > 1, "Неверно задано значение MAX_FEED");
#define c  250000 / ((uint32_t)MIN_aFEED * MOTOR_Z_STEP_PER_REV * McSTEP_Z / ((uint32_t)60 * SCREW_Z / 100) * 2) -1
static_assert(c <= 65535, "Неверно задано значение MIN_aFEED");
#define d  250000 / ((uint32_t)MAX_aFEED * MOTOR_Z_STEP_PER_REV * McSTEP_Z / ((uint32_t)60 * SCREW_Z / 100) * 2) -1
static_assert(d > 1, "Неверно задано значение MAX_aFEED");

#define e  (uint32_t)(ENC_LINE_PER_REV / ((float)MOTOR_X_STEP_PER_REV * McSTEP_X * MIN_FEED / SCREW_X) /2 +0.5)
static_assert(e <= 255, "Неверно задано значение MIN_FEED");
#define f  (uint32_t)(ENC_LINE_PER_REV / ((float)MOTOR_X_STEP_PER_REV * McSTEP_X * MAX_FEED / SCREW_X) /2 +0.5)
static_assert(f > 1, "Неверно задано значение MAX_FEED");
#define g  250000 / ((uint32_t)MIN_aFEED * MOTOR_X_STEP_PER_REV * McSTEP_X / ((uint32_t)60 * SCREW_X / 100) * 2) -1
static_assert(g <= 65535, "Неверно задано значение MIN_aFEED");
#define h  250000 / ((uint32_t)MAX_aFEED * MOTOR_X_STEP_PER_REV * McSTEP_X / ((uint32_t)60 * SCREW_X / 100) * 2) -1
static_assert(h > 1, "Неверно задано значение MAX_aFEED");
//////////////////////////////////////////////////////////


// ***** MY CONSTANT *****
#define CW               0
#define CCW              1
#ifdef Z_INVERT
  #define ZCW              1
  #define ZCCW             0
#else
  #define ZCW              0
  #define ZCCW             1
#endif
#define ON               1
#define OFF              0


// ***** LCD *****
#include <LiquidCrystal.h>
LiquidCrystal lcd(8, 9, 10, 11, 12, 13);
char LCD_Row_1[17];
char LCD_Row_2[17];

#define Beeper_Init()          DDRH = B01100010;\
                               PORTH = B10011101    // LCD-H5,H6 Buzzer-PH1_Pin16
#define Beeper_On()            PORTH &= ~(1<<1)     // Pin16 0
#define Beeper_Off()           PORTH |= (1<<1)      // Pin16 1



// ***** Stepper Motor *****
#define Motor_Init()           DDRL = B11111011;\
                               PORTL = B0000100

#define Motor_Z_SetPulse()     PORTL &= ~(1<<0)     // Pin49 0
#define Motor_Z_RemovePulse()  PORTL |= (1<<0)      // Pin49 1
#define Motor_Z_InvertPulse()  PORTL ^= (1<<0)      // Pin49
#define Read_Z_State           (PINL & (1<<0))

#define Motor_X_SetPulse()     PORTL &= ~(1<<1)     // Pin48 0
#define Motor_X_RemovePulse()  PORTL |= (1<<1)      // Pin48 1
#define Motor_X_InvertPulse()  PORTL ^= (1<<1)      // Pin48
#define Read_X_State           (PINL & (1<<1))

#ifdef Z_INVERT
  #define Motor_Z_CCW()           PORTL &= ~(1<<6)    // Pin43 0
  #define Motor_Z_CW()          PORTL |= (1<<6)     // Pin43 1
#else
  #define Motor_Z_CW()           PORTL &= ~(1<<6)    // Pin43 0
  #define Motor_Z_CCW()          PORTL |= (1<<6)     // Pin43 1
#endif

#define Motor_X_CW()           PORTL &= ~(1<<5)    // Pin44 0
#define Motor_X_CCW()          PORTL |= (1<<5)     // Pin44 1

#ifdef Z_ENA_INVERT
  #define Motor_Z_Enable()   do {PORTL &= ~(1<<4); _delay_ms(120);} while(0)  // Pin45 0
  #define Motor_Z_Disable()      PORTL |= (1<<4)                              // Pin45 1
  #define Read_Z_Ena_State       !(PINL & (1<<4))
#else
  #define Motor_Z_Enable()   do {PORTL |= (1<<4); _delay_ms(120);} while(0)   // Pin45 1
  #define Motor_Z_Disable()      PORTL &= ~(1<<4)                             // Pin45 0
  #define Read_Z_Ena_State       (PINL & (1<<4))
#endif

#define Motor_X_Enable()   do {PORTL |= (1<<3); _delay_ms(120);} while(0)   // Pin46 1
#define Motor_X_Disable()      PORTL &= ~(1<<3)                             // Pin46 0
#define Read_X_Ena_State       (PINL & (1<<3))


// ***** Tacho *****
#define TachoSetPulse()        PORTL |= (1<<7)      // Pin42 1
#define TachoRemovePulse()     PORTL &= ~(1<<7)     // Pin42 0


// ***** Encoder *****
#define ENC_TICK              (ENC_LINE_PER_REV * 2)    // Рабочее кол-во импульсов
#define Encoder_Init()         DDRD = B00000000;\
                               PORTD = B11111111        // подтяжка PIN_21, 20, 19, 18
#define Enc_Read              (PIND & (1<<1))
#define Enc_Ch_A              (PIND & (1<<0))
#define Enc_Ch_B              (PIND & (1<<1))
 


// ***** Hand_Coder *****            // Z/X: Input-E4,E5, подтяжка-E4,E5, X1/X10: Input-J0,J1, подтяжка-J0,J1.
#define Hand_Init()            DDRE = B00000000;\
                               PORTE = B11111111;\
                               DDRJ = B00000000;\
                               PORTJ = B11111111
                                     
#define Hand_Ch_A             (PIND & (1<<2))
#define Hand_Ch_B             (PIND & (1<<3))

#define Hand_Axis_Read        (PINE & B00110000)       // E4,E5
byte Hand_Axis_Old = 0;

#define Hand_Scale_Read        (PINJ & B00000011)      // J0,J1
byte Hand_Scale_Old = 0;


//***** Limit Buttons & LEDs *****
#define Limit_Init()           DDRA = B10101010;\
                               PORTA = B01010101    // IN-A0,A2,A4,A6, OUT-A1,A3,A5,A7, подтяжка

#define Limit_Buttons_Read    (PINA & B01010101)    // PA0 Pin22, PA2 Pin24, PA4 Pin26, PA6 Pin28.
byte Limit_Button_Old = 0;

#define Limit_Rear_LED_On()    PORTA &= ~(1<<1)     // PA1, Pin23 0
#define Limit_Rear_LED_Off()   PORTA |= (1<<1)      // PA1, Pin23 1
#define Limit_Front_LED_On()   PORTA &= ~(1<<3)     // PA3, Pin25 0
#define Limit_Front_LED_Off()  PORTA |= (1<<3)      // PA3, Pin25 1
#define Limit_Right_LED_On()   PORTA &= ~(1<<5)     // PA5, Pin27 0
#define Limit_Right_LED_Off()  PORTA |= (1<<5)      // PA5, Pin27 1
#define Limit_Left_LED_On()    PORTA &= ~(1<<7)     // PA7, Pin29 0
#define Limit_Left_LED_Off()   PORTA |= (1<<7)      // PA7, Pin29 1

#define Limit_Pos_Max          1073741824
#define Limit_Pos_Min         -1073741824


//////////////////
#define Menu_Buttons_Init()    DDRF = B00000000;\
                               PORTF = B11111111;     

#define Buttons_Read           (PINF & B00001111)    // Pin_A0 PF0, Pin_A1 PF1, Pin_A2 PF2, Pin_A3 PF3, Pin_A4 PF4.
byte Button_Old = 0;

#define Button_Sel_Read        (PINF & B00010000)    // Pin_A4 PF4
byte Button_Sel_Old = 0;
bool key_sel_flag = false;

//////////////////
#define Joy_Init()             DDRK = B00000000;\
                               PORTK = B11111111;    // подтяжка PIN_A8, A9, A10, A11, A12 // Submode Sw: A13, A14, A15

#define Joy_Read              (PINK & B00001111)     // PK0 PK1 PK2 PK3
#define Button_Rapid          (PINK & B00010000)     // PK4
byte Joy_Old = 0;

////////////////////
#define Submode_Read          (PINK & B11100000)     // PK5 PK6 PK7
byte Submode_Old = 0;


// ***** Mode *****
#define Mode_Switch_Init()     DDRC = B00000000;\
                               PORTC = B11111111;        // подтяжка PORT_A, ОБЯЗАТЕЛЬНА! внешняя подтяжка к +5 через 1К резисторы
#define Mode_Read             (PINC & B11111111)
byte Mode_Old = 0;


enum Mode
{
  Mode_Thread = 1,
  Mode_Feed,
  Mode_aFeed,
  Mode_Cone_L,
  Mode_Cone_R,
  Mode_Reserve,
  Mode_Sphere,
  Mode_Divider
};

enum Sub_Mode_Thread
{
  Sub_Mode_Thread_Int = 1,
  Sub_Mode_Thread_Man,
  Sub_Mode_Thread_Ext,
};

enum Sub_Mode_Feed
{
  Sub_Mode_Feed_Int = 1,
  Sub_Mode_Feed_Man,
  Sub_Mode_Feed_Ext,
};

enum Sub_Mode_aFeed
{
  Sub_Mode_aFeed_Int = 1,
  Sub_Mode_aFeed_Man,
  Sub_Mode_aFeed_Ext,
};

enum Sub_Mode_Cone
{
  Sub_Mode_Cone_Int = 1,
  Sub_Mode_Cone_Man,
  Sub_Mode_Cone_Ext,
};

enum Sub_Mode_Sphere
{
  Sub_Mode_Sphere_Int = 1,
  Sub_Mode_Sphere_Man,
  Sub_Mode_Sphere_Ext,
};


//***** Ускоренное перемещение *****
#define Timer2_Init()          TCCR2A = (1<<WGM21);\
                               TCCR2B = (1<<CS20)|(1<<CS21); // 16MHz/32 = 500kHz

//***** РГИ перемещение *****
#define Timer3_Init()          TCCR3A = 0;\
                               TCCR3B = (1<<WGM32)|(1<<CS30)|(1<<CS31); // 16MHz/32 = 250kHz

// ***** aFeed *****
#define Timer4_Init()          TCCR4A = 0;\
                               TCCR4B = (1<<WGM42)|(1<<CS40)|(1<<CS41); // 16MHz/32 = 250kHz

// ***** Feed *****
#define Timer5_Init()          TCCR5A = 0;\
                               TCCR5B = (1<<WGM52) | (1<<CS52) | (1<<CS51) | (1<<CS50)


// ***** Cone *****
struct cone_info_type
{
  byte Cs_Div;
  int  Cm_Div;
  char Cone_Print[6];
};
// This table must be re-calculated each time hardware parameters
//  at the top change. Use tables.html to find the new values.
const cone_info_type Cone_Info[] = {
  {  0, 8400, "45dg"},
  { 32, 2762, " KM0"}, // 1:19.212
  { 33, 6790, " KM1"}, // 1:20.047
  { 33, 6336, " KM2"}, // 1:20.02
  { 33, 4690, " KM3"}, // 1:19.922
  { 32, 3467, " KM4"}, // 1:19.254
  { 31, 9234, " KM5"}, // 1:19.002
  { 32, 2224, " KM6"}, // 1:19.18
  {  6, 7200, " 1:4"}, // 1:4
  {  8, 4000, " 1:5"}, // 1:5
  { 11, 7600, " 1:7"}, // 1:7
  { 16, 8000, "1:10"}, // 1:10
  { 26, 8800, "1:16"}, // 1:16
  { 33, 6000, "1:20"}, // 1:20
  { 40, 3200, "1:24"}, // 1:24
  { 50, 4000, "1:30"}, // 1:30
  { 84,    0, "1:50"}, // 1:50
  { 15, 3600, "7:64"}, // 7:64
  {  5, 9769, " 8dg"},
  {  4, 7639, "10dg"},
  {  3, 1349, "15dg"},
  {  1, 4549, "30dg"},
};
#define TOTAL_CONE (sizeof(Cone_Info) / sizeof(Cone_Info[0]))


// ***** Threads *****
struct thread_info_type
{
  byte Ks_Div_Z;
  int  Km_Div_Z;
  byte Ks_Div_X;
  int  Km_Div_X;
  char Thread_Print[7];
  float Step;
  byte Pass;
  char Limit_Print[8];
};
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
void loop()
{
  Spindle();
  Read_ADC_Feed();
  if (KEYB_TIMER_FLAG != 0) Menu();
  
  if (Mode == Mode_Divider) Print(); // пока для теста !!!!!!!!!!!!!!!!!!!!!!!!!!!!!!!!!!!!!!!!!!!
//  Print();                         // тоько для теста !!!!!!!!!!!!!!!!!!!!!!!!!!!!!!!!!!!!!!!!!!

}


//////////////////////////////////////////////////////////////////////////////////////////////////////////////////////////////////////
//////////////////////////////////////////////////////////////////////////////////////////////////////////////////////////////////////
// *****  Thread ***** ///////////////////////////////////////////////////////////////////////////////////////////////////////////////
//////////////////////////////////////////////////////////////////////////////////////////////////////////////////////////////////////
//////////////////////////////////////////////////////////////////////////////////////////////////////////////////////////////////////
ISR(INT0_vect)
{
   TachoRemovePulse();

   if (!Enc_Ch_A)
   {
      if (!Enc_Ch_B)
      {
         Spindle_Dir = CW;
         if (++Enc_Pos == ENC_TICK)
         {                                           
            Enc_Pos = 0;
            TachoSetPulse();
            if (Joy_Z_flag == ON) {Step_Z_flag = ON;}
            else if (Joy_X_flag == ON) {Step_X_flag = ON;}
         }
      }
      else
      {
        Spindle_Dir = CCW;
        if (--Enc_Pos < 0)
        { 
           Enc_Pos = ENC_TICK - 1;
           TachoSetPulse();
           if (Joy_Z_flag == ON) {Step_Z_flag = ON;}
           else if (Joy_X_flag == ON) {Step_X_flag = ON;}
        }
      }
   }
   
   else
   {
      if (!Enc_Ch_B) 
      {
         Spindle_Dir = CCW;
         if (--Enc_Pos < 0)
         { 
            Enc_Pos = ENC_TICK - 1;
            TachoSetPulse();
            if (Joy_Z_flag == ON) {Step_Z_flag = ON;}
            else if (Joy_X_flag == ON) {Step_X_flag = ON;}
         }
      }
      else 
      {
         Spindle_Dir = CW;
         if (++Enc_Pos == ENC_TICK)
         {                                           
            Enc_Pos = 0;
            TachoSetPulse();
            if (Joy_Z_flag == ON) {Step_Z_flag = ON;}
            else if (Joy_X_flag == ON) {Step_X_flag = ON;}
         }
      }
   }  
   
   if (Step_Z_flag == ON)
   {   Motor_Z_RemovePulse();
      if ( (Motor_Z_Dir == ZCW && Motor_Z_Pos > Limit_Pos) || (Motor_Z_Dir == ZCCW && Motor_Z_Pos < Limit_Pos) || (!Joy_Z_flag) )
      {
         if (tmp_Ks_Divisor < tmp_Accel)
         {
            Ks_Count++;
            if (Ks_Count > tmp_Ks_Divisor)
            {
               Motor_Z_SetPulse();
               if (Motor_Z_Dir == ZCW) {Motor_Z_Pos ++;}
               else {Motor_Z_Pos --;}
               Ks_Count = 0;
               if (++Repeat_Count == REPEAt)
               {
                  Repeat_Count = 0;
                  tmp_Ks_Divisor ++;
               }
            }
         }  
         else {Step_Z_flag = OFF;}
      }

      else
      {
         Ks_Count++;
         if (Ks_Count > tmp_Ks_Divisor)
         {
            Motor_Z_SetPulse();
            if (Motor_Z_Dir == ZCW) {Motor_Z_Pos ++;}
            else {Motor_Z_Pos --;}
         
            if (tmp_Ks_Divisor > Ks_Divisor)
            {
               Ks_Count = 0;
               if (++Repeat_Count == REPEAt)
               {
                  Repeat_Count = 0;
                  tmp_Ks_Divisor --;
               }
            }
            else
            {  
               Km_Count = Km_Count + Km_Divisor;
               if (Km_Count > Km_Divisor)
               {
                  Km_Count = Km_Count - 10000;
                  Ks_Count = 0;
               }
               else {Ks_Count = 1;}
            }
         }
      }
   }
   
   if (Step_X_flag == ON)
   {  Motor_X_RemovePulse();
      if ( (Motor_X_Dir == CW && Motor_X_Pos > Limit_Pos) || (Motor_X_Dir == CCW && Motor_X_Pos < Limit_Pos) || (!Joy_X_flag) )
      {
         if (tmp_Ks_Divisor < tmp_Accel)
         {
            Ks_Count++;
            if (Ks_Count > tmp_Ks_Divisor)
            {
               Motor_X_SetPulse();
               if (Motor_X_Dir == CW) {Motor_X_Pos ++;}
               else {Motor_X_Pos --;}
               Ks_Count = 0;
               if (++Repeat_Count == REPEAt)
               {
                  Repeat_Count = 0;
                  tmp_Ks_Divisor ++;
               }
            }
         }  
         else {Step_X_flag = OFF;}
      }

      else
      {
         Ks_Count++;
         if (Ks_Count > tmp_Ks_Divisor)
         {
            Motor_X_SetPulse();
            if (Motor_X_Dir == CW) {Motor_X_Pos ++;}
            else {Motor_X_Pos --;}
         
            if (tmp_Ks_Divisor > Ks_Divisor)
            {
               Ks_Count = 0;
               if (++Repeat_Count == REPEAt)
               {
                  Repeat_Count = 0;
                  tmp_Ks_Divisor --;
               }
            }
            else
            {  
               Km_Count = Km_Count + Km_Divisor;
               if (Km_Count > Km_Divisor)
               {
                  Km_Count = Km_Count - 10000;
                  Ks_Count = 0;
               }
               else {Ks_Count = 1;}
            }
         }
      }
   }
}


ISR(INT1_vect)
{
   //
}


//////////////////////////////////////////////////////////////////////////////////////////////////////////////////////////////////////
//////////////////////////////////////////////////////////////////////////////////////////////////////////////////////////////////////
// *****  Tacho ***** ////////////////////////////////////////////////////////////////////////////////////////////////////////////////
//////////////////////////////////////////////////////////////////////////////////////////////////////////////////////////////////////
//////////////////////////////////////////////////////////////////////////////////////////////////////////////////////////////////////
ISR (TIMER0_COMPB_vect)                                 // Тахометр
{
   //   
}


//////////////////////////////////////////////////////////////////////////////////////////////////////////////////////////////////////
//////////////////////////////////////////////////////////////////////////////////////////////////////////////////////////////////////
// *****  Feed & Cone ***** //////////////////////////////////////////////////////////////////////////////////////////////////////////
//////////////////////////////////////////////////////////////////////////////////////////////////////////////////////////////////////
//////////////////////////////////////////////////////////////////////////////////////////////////////////////////////////////////////
ISR (TIMER5_COMPA_vect)
{
   if (Joy_Z_flag == ON) {Motor_X_RemovePulse();}
   TachoRemovePulse();
   Tacho_Count = Tacho_Count + (OCR5A+1);
   if (Tacho_Count > ENC_LINE_PER_REV)
   {
      TachoSetPulse();
      Tacho_Count = Tacho_Count - ENC_LINE_PER_REV;
   }
   
   if ( (Motor_Z_Dir == ZCW && Motor_Z_Pos > Limit_Pos) || (Motor_Z_Dir == ZCCW && Motor_Z_Pos < Limit_Pos) || (!feed_Z_flag) )
   {
      if (OCR5A < max_OCR5A)
      {
         Motor_Z_InvertPulse();
         if (!Read_Z_State)
         {
            OCR5A++;
            if (Motor_Z_Dir == ZCW) {Motor_Z_Pos ++;}
            else {Motor_Z_Pos --;}
         }
      }
      else
      {             
         Step_Z_flag = OFF;
         Step_X_flag = OFF;
      }
   }
   
   else
   {
      Step_Z_flag = ON;
      Motor_Z_InvertPulse();
      if (!Read_Z_State)
      {
         if (Motor_Z_Dir == ZCW) {Motor_Z_Pos ++;}
         else {Motor_Z_Pos --;}
      
         if (OCR5A > Feed_Divisor) {OCR5A--;}
         else if (OCR5A < Feed_Divisor) {OCR5A ++;}
      }
   }
   
   if (Step_X_flag == ON)
   {
      if (++Cs_Count > Cs_Divisor)
      {
         Motor_X_SetPulse();

         if (Motor_X_Dir == CW) {Motor_X_Pos ++;}
         else {Motor_X_Pos --;}

         Cm_Count = Cm_Count + Cm_Divisor;
         if (Cm_Count > Cm_Divisor)
         {
            Cm_Count = Cm_Count - 10000;
            Cs_Count = 0;
         }
         else {Cs_Count = 1;}
      }
   }
}
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

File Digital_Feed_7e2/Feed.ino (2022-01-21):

//////////////////////////////////////////////////////////////////////////////////////////////////////////////////////////////////////
//////////////////////////////////////////////////////////////////////////////////////////////////////////////////////////////////////
// ********** Режим "Подача" ********** //////////////////////////////////////////////////////////////////////////////////////////////
//////////////////////////////////////////////////////////////////////////////////////////////////////////////////////////////////////
//////////////////////////////////////////////////////////////////////////////////////////////////////////////////////////////////////
void Feed_Left(bool & a_flag, bool & b_flag)
{
   if (b_flag == true) return;
   a_flag = false;
   b_flag = true;

   Joy_X_flag = OFF;
   feed_X_flag = OFF;
   Start_Speed = ENC_LINE_PER_REV / ((float)MOTOR_Z_STEP_PER_REV * McSTEP_Z * MIN_FEED / SCREW_Z) / FEED_ACCEL /2 +0.5;
   if (Motor_Z_Pos < Limit_Pos_Left - Start_Speed * 2)
   {
      Feed_Divisor = ENC_LINE_PER_REV / ((float)MOTOR_Z_STEP_PER_REV * McSTEP_Z * Feed_mm / SCREW_Z) /2 +0.5;
      if (Feed_Divisor < Start_Speed)
      {
         max_OCR5A = Start_Speed;
         if (Step_Z_flag == OFF)
         {
            OCR5A = Start_Speed;
         }
      }
      else
      {
         max_OCR5A = Feed_Divisor;
         OCR5A = Feed_Divisor;
      }
   }
   else
   {
      Feed_Divisor = Start_Speed;
      max_OCR5A = Start_Speed;
      OCR5A = Start_Speed;
   }
   
   Brake_Compens = max_OCR5A - Feed_Divisor + 1;
   Limit_Pos = Limit_Pos_Left - Brake_Compens;

   Motor_Z_Dir = ZCW;
   Motor_Z_CW();
   if (Read_Z_Ena_State == false) Motor_Z_Enable();
   
   feed_Z_flag = ON;
   Joy_Z_flag = ON;
   Ena_INT_Z_Feed();
}

void Feed_Right(bool & a_flag, bool & b_flag)
{
   if (b_flag == true) return;
   a_flag = false;
   b_flag = true;

   Joy_X_flag = OFF;
   feed_X_flag = OFF;
   Start_Speed = ENC_LINE_PER_REV / ((float)MOTOR_Z_STEP_PER_REV * McSTEP_Z * MIN_FEED / SCREW_Z) / FEED_ACCEL /2 +0.5;
   if (Motor_Z_Pos > Limit_Pos_Right + Start_Speed * 2)
   {
      Feed_Divisor = ENC_LINE_PER_REV / ((float)MOTOR_Z_STEP_PER_REV * McSTEP_Z * Feed_mm / SCREW_Z) /2 +0.5;
      if (Feed_Divisor < Start_Speed)
      {
         max_OCR5A = Start_Speed;
         if (Step_Z_flag == OFF)
         {
            OCR5A = Start_Speed;
         }
      }
      else
      {
         max_OCR5A = Feed_Divisor;
         OCR5A = Feed_Divisor;
      }
   }
   else
   {
      Feed_Divisor = Start_Speed;
      max_OCR5A = Start_Speed;
      OCR5A = Start_Speed;
   }
   
   Brake_Compens = (max_OCR5A - Feed_Divisor) + 1;
   Limit_Pos = Limit_Pos_Right + Brake_Compens;

   Motor_Z_Dir = ZCCW;
   Motor_Z_CCW();
   if (Read_Z_Ena_State == false) Motor_Z_Enable();
   
   feed_Z_flag = ON;
   Joy_Z_flag = ON;
   Ena_INT_Z_Feed();
}

void Feed_Front(bool & a_flag, bool & b_flag)
{  
   if (b_flag == true) return;
   a_flag = false;
   b_flag = true;

   Joy_Z_flag = OFF;
   feed_Z_flag = OFF;
   Start_Speed = ENC_LINE_PER_REV / ((float)MOTOR_X_STEP_PER_REV * McSTEP_X * MIN_FEED / SCREW_X) / FEED_ACCEL /2 +0.5;
   if (Motor_X_Pos < Limit_Pos_Front - Start_Speed * 2)
   {
      Feed_Divisor = ENC_LINE_PER_REV / ((float)MOTOR_X_STEP_PER_REV * McSTEP_X * Feed_mm / SCREW_X) /2 +0.5;
      if (Feed_Divisor < Start_Speed)
      {
         max_OCR5A = Start_Speed;
         if (Step_X_flag == OFF)
         {
            OCR5A = Start_Speed;
         }
      }
      else
      {
         max_OCR5A = Feed_Divisor;
         OCR5A = Feed_Divisor;
      }
   }
   else
   {
      Feed_Divisor = Start_Speed;
      max_OCR5A = Start_Speed;
      OCR5A = Start_Speed;
   }
   
   Brake_Compens = max_OCR5A - Feed_Divisor + 1;
   Limit_Pos = Limit_Pos_Front - Brake_Compens;

   Motor_X_Dir = CW;
   Motor_X_CW();
   if (Read_X_Ena_State == false) Motor_X_Enable();
   
   feed_X_flag = ON;
   Joy_X_flag = ON;
   Ena_INT_X_Feed();
   
}

void Feed_Rear(bool & a_flag, bool & b_flag)
{
   if (b_flag == true) return;
   a_flag = false;
   b_flag = true;

   Joy_Z_flag = OFF;
   feed_Z_flag = OFF;
   Start_Speed = ENC_LINE_PER_REV / ((float)MOTOR_X_STEP_PER_REV * McSTEP_X * MIN_FEED / SCREW_X) / FEED_ACCEL /2 +0.5;
   if (Motor_X_Pos > Limit_Pos_Rear + Start_Speed * 2)
   {
      Feed_Divisor = ENC_LINE_PER_REV / ((float)MOTOR_X_STEP_PER_REV * McSTEP_X * Feed_mm / SCREW_X) /2 +0.5;
      if (Feed_Divisor < Start_Speed)
      {
         max_OCR5A = Start_Speed;
         if (Step_X_flag == OFF)
         {
            OCR5A = Start_Speed;
         }
      }
      else
      {
         max_OCR5A = Feed_Divisor;
         OCR5A = Feed_Divisor;
      }
   }
   else
   {
      Feed_Divisor = Start_Speed;
      max_OCR5A = Start_Speed;
      OCR5A = Start_Speed;
   }

   Brake_Compens = max_OCR5A - Feed_Divisor + 1;
   Limit_Pos = Limit_Pos_Rear + Brake_Compens;

   Motor_X_Dir = CCW;
   Motor_X_CCW();
   if (Read_X_Ena_State == false) Motor_X_Enable();
   
   feed_X_flag = ON;
   Joy_X_flag = ON;
   Ena_INT_X_Feed();
}


//////////////////////////////////////////////////////////////////////////////////////////////////////////////////////////////////////
//////////////////////////////////////////////////////////////////////////////////////////////////////////////////////////////////////
// ********** Режим "Быстрая Подача" ********** //////////////////////////////////////////////////////////////////////////////////////
//////////////////////////////////////////////////////////////////////////////////////////////////////////////////////////////////////
//////////////////////////////////////////////////////////////////////////////////////////////////////////////////////////////////////
void Rapid_Feed_Left(bool & a_flag, bool & b_flag)
{
   if (a_flag == true) return;
   b_flag = false;
   a_flag = true;

   Joy_X_flag = OFF;
   feed_X_flag = OFF;
   rapid_X_flag = OFF;
   Brake_Compens = (MIN_RAPID_MOTION - MAX_RAPID_MOTION) * REPEAt + 1;
   Limit_Pos = Limit_Pos_Left - Brake_Compens;

   Motor_Z_Dir = ZCW;
   Motor_Z_CW();
   if (Read_Z_Ena_State == false) Motor_Z_Enable();
   
   Joy_Z_flag = ON;             
   rapid_Z_flag = ON;
   Ena_INT_Z_Rapid();
}

void Rapid_Feed_Right(bool & a_flag, bool & b_flag)
{
   if (a_flag == true) return;
   b_flag = false;
   a_flag = true;

   Joy_X_flag = OFF;
   feed_X_flag = OFF;
   rapid_X_flag = OFF;
   Brake_Compens = (MIN_RAPID_MOTION - MAX_RAPID_MOTION) * REPEAt + 1;
   Limit_Pos = Limit_Pos_Right + Brake_Compens;

   Motor_Z_Dir = ZCCW;
   Motor_Z_CCW();
   if (Read_Z_Ena_State == false) Motor_Z_Enable();
   
   Joy_Z_flag = ON;
   rapid_Z_flag = ON;
   Ena_INT_Z_Rapid();
}
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

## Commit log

2021-12-17 Adding more PCB files
2021-12-23 Adding 3d models of cases
    [MegaElsCase.f3d, MegaElsMPG.f3d, megaels-case-body.stl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]
2022-01-17 Control labels printout
2022-01-21 Adding support for Z invertion, updating hardware params
    [!_Calc_v7e.ods]
2022-01-28 Support inverting Z enable signal, more translations
    [Digital_Feed_7e2.ino]
2022-01-30 Case update and translated XLS files
    [!_Calc_v7e.ods, !_Calc_v7e.xls, MegaElsCase.f3d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]
2022-01-30 Replace XLS-based cone/thread table calculation with a simpler method based on tables.html
    [!_Calc_v7e.ods, !_Calc_v7e.xls]
2022-02-05 Update HandCoder.ino
    change z direction encoder
